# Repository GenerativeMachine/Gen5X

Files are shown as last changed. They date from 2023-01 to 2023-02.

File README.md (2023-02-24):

# Gen5X
Gen5X
Repo for the development of the Gen5X open hardware generatively designed 5 axis 3D printer. 

Imagine a world where machines not only have the ability to design and manufacture products, but they can also create their own updates and upgrades, without any human intervention. The Gen5X is an open-source project aiming to develop self-designing, rapid replicating machines. This repo aims to serve as a resource for researchers in the fields of computational design, AM, and Mechanical Engineering. By open-sourcing this project we hope to foster innovation within the community, and invite you to join us in pushing the boundaries of what is possible with generative design, 3D printing technology, and AI. 

Fusion360 link: https://a360.co/3Y41ZV0 
GrabCAD: STEP files to be uploaded this weekend. 

<p align="center">
  
</p>

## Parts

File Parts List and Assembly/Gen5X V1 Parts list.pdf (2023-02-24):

# Gen5X V1.0

## Parts List

This list of parts includes everything needed to build and assemble the Gen5X Generatively Designed 3D Printer. The V1.0 was designed to work with readily available low cost components. Many of the parts required for this build can be salvaged from older 3D Printers, or similar projects. If you don’t have the right parts (for example LM10UU bearings and 10mm steel rods instead of the specified LM8UU) you could have a go at regenerating the design in Fusion360 to work with your components.

The Fusion360 file can be accessed here: https://a360.co/3Y41ZV0

STEP files have now also been added to the project repo.

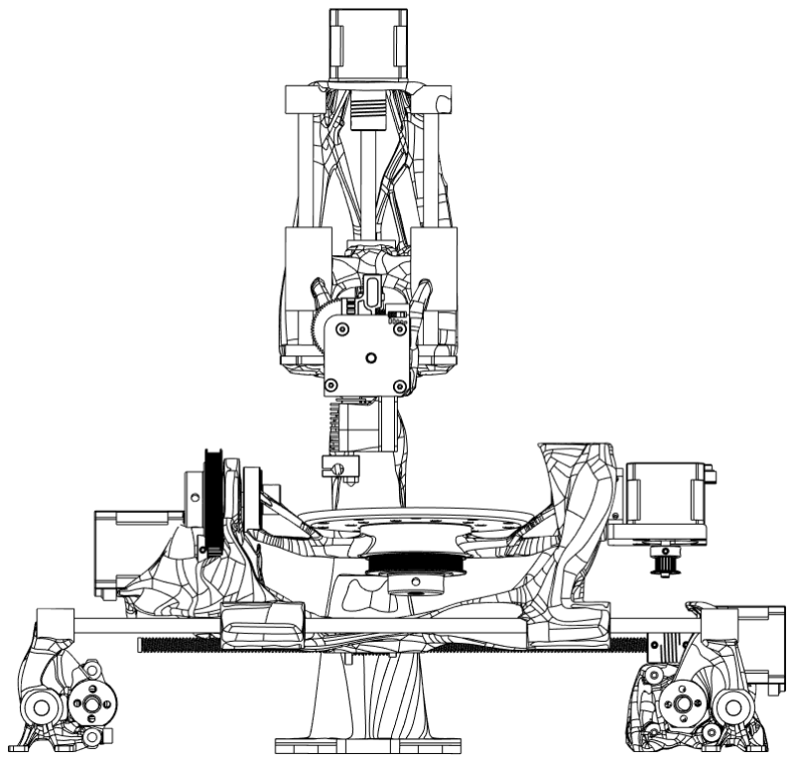
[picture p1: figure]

## Sub-Assemblies

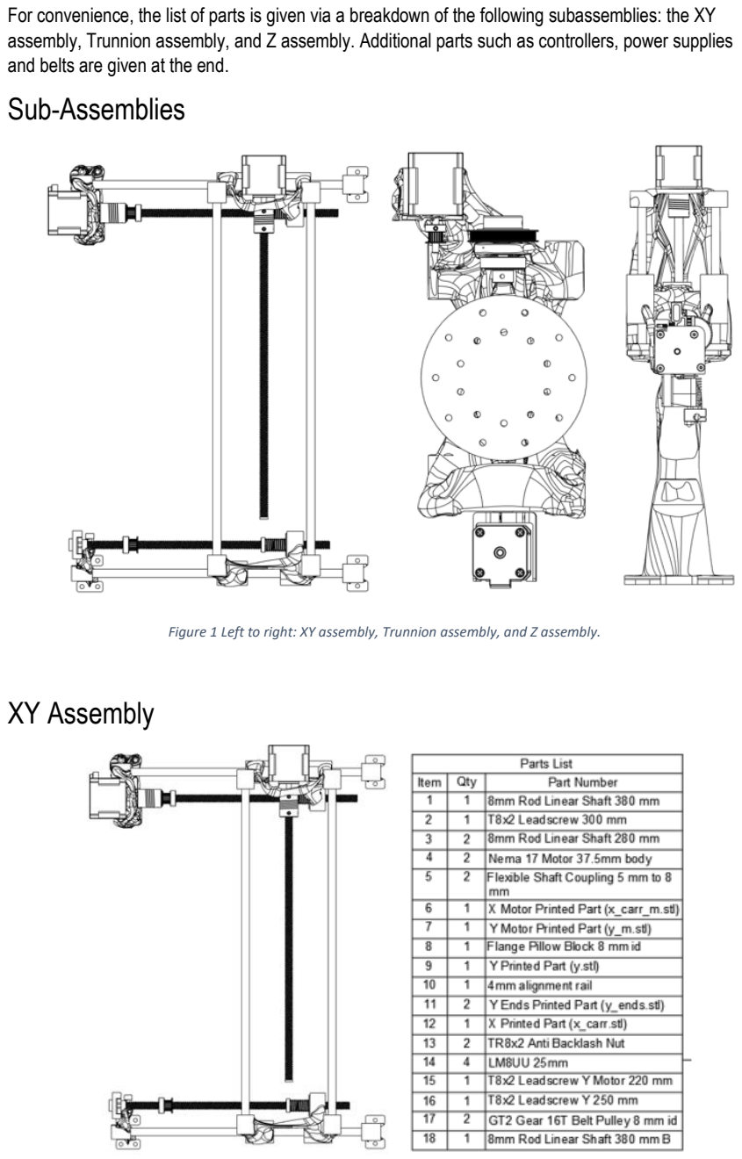
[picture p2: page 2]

For convenience, the list of parts is given via a breakdown of the following subassemblies: the XY assembly, Trunnion assembly, and Z assembly. Additional parts such as controllers, power supplies and belts are given at the end.

Figure 1 Left to right: XY assembly, Trunnion assembly, and Z assembly.

## XY Assembly

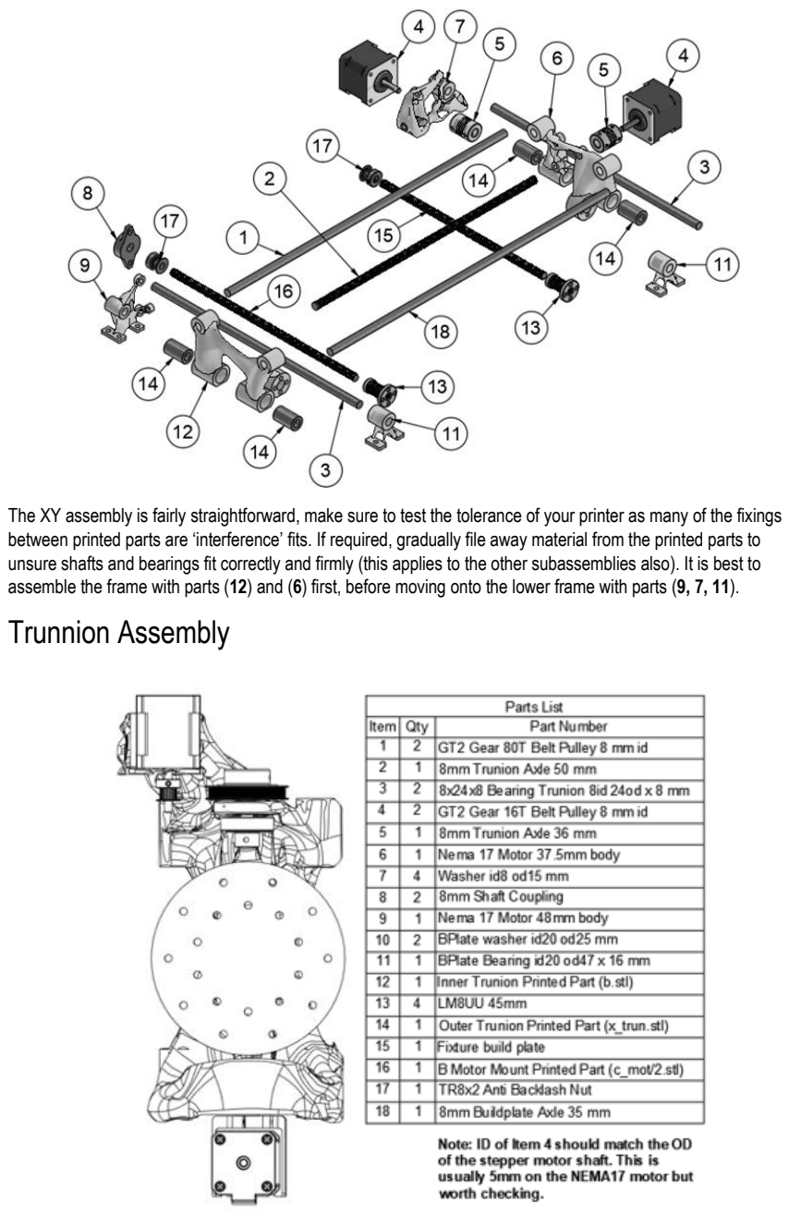
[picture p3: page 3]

The XY assembly is fairly straightforward, make sure to test the tolerance of your printer as many of the fixings between printed parts are ‘interference’ fits. If required, gradually file away material from the printed parts to unsure shafts and bearings fit correctly and firmly (this applies to the other subassemblies also). It is best to assemble the frame with parts (12) and (6) first, before moving onto the lower frame with parts (9, 7, 11).

## Trunnion Assembly

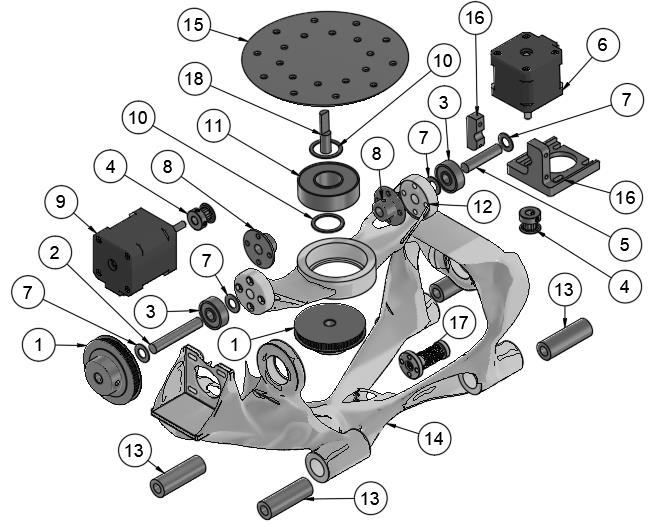
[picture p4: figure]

To assemble the trunnion, firstly press the bearings (3) into the outer trunnion (14) ensuring that the fit is firm. Next, assemble the inner trunnion (12, 8, 11). Fixing (8) to (12) will require four nuts pressed into part (12); using a soldering iron to press these will ensure that the nuts are secure. With part (8) in place, position part (12) between the mounting points in the inner trunnion with spacer washers (7) on the outside (between 12 and 3). Push the respective axles (2, 5) through parts (3) until flush with part (8) and secure.

## Z Assembly and Hotend

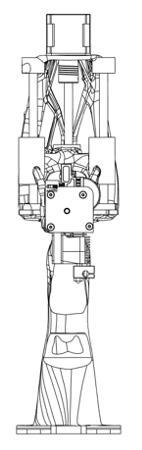
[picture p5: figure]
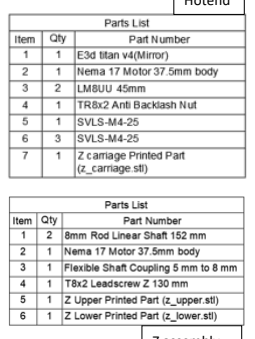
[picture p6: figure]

Z assembly

Hotend

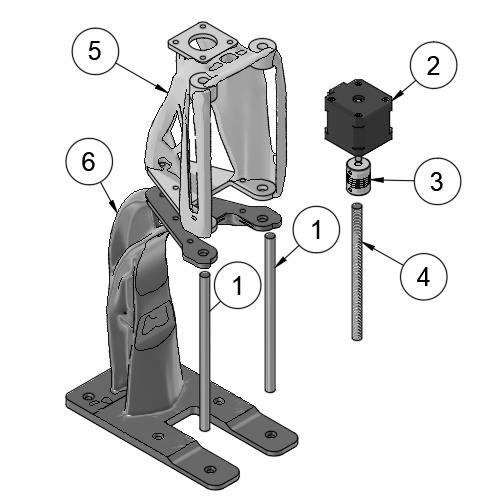
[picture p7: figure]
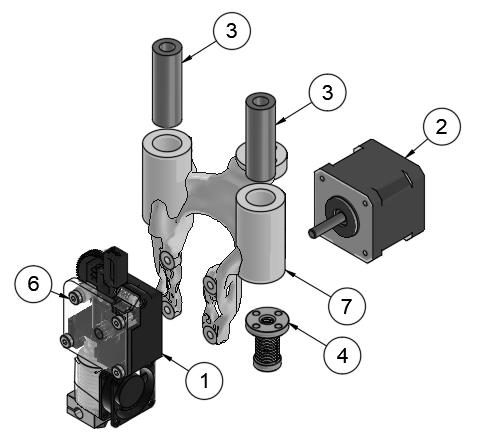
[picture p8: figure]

The Z axis is split into two parts (5, 6) to allow for printing on a broader range of machines. To print the Z axis whole a generative study would need to be redefined as a single piece. Alternatively, parts (5, 6) could be merged in meshmixer before printing. The two parts (5, 6) are currently fastened using M3 or M4 nuts and bolts. Mounting the hotend assembly into the Z axis (5) can be achieved by threading the leadscrew (4) into the hotend backlash nut (hotend 4) before fitting onto half inserted linear shafts (1). Once in place shafts (1) can be pushed though into their positions on part (6). The motor coupling (3) and motor (2) can then be fixed to part (5).

## Electronics


## Belts and Fasteners


(accurate quantities for bolts will soon be given)

Duet 2
DueX5


Meanwell 24v 350W 14.6Amp Power Supply

Belts (Closed Loop) | Qty | Fasteners | Qty
Turntable belt (376 mm) | 1 | M3x8 mm socket head bolts and washers | 40
Trunnion belt (224 mm) | 1 | M3 and M4 Nyloc nuts | 20
Y axis belt (670 mm) | 1 | Assorted length M3 and M4 bolts (10 to 40 mm) | xx

Hotend assembly

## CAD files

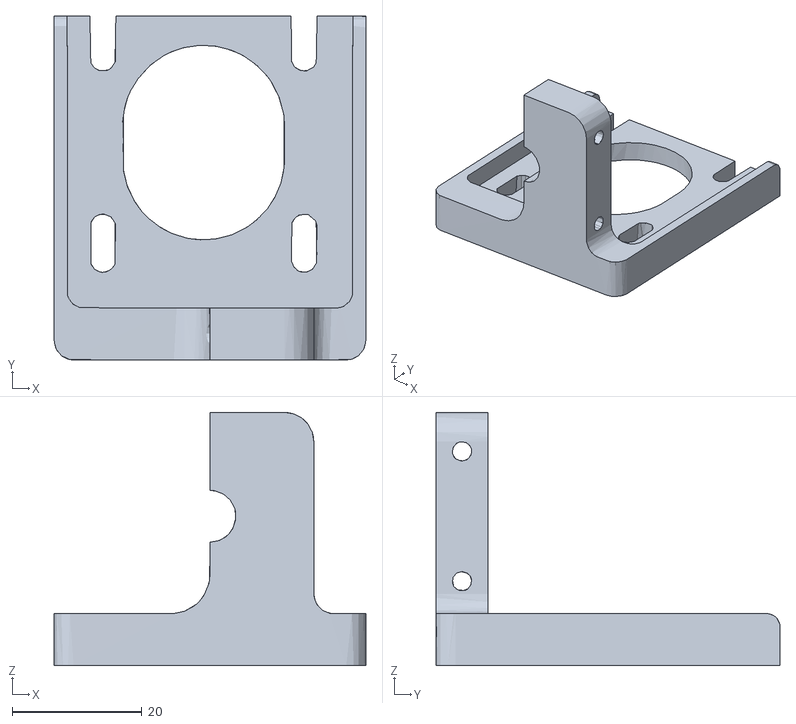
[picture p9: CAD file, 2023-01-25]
Gen5X V1 STL Files/BC Axis/c_mot.stl
48.0 x 53.0 x 39.0

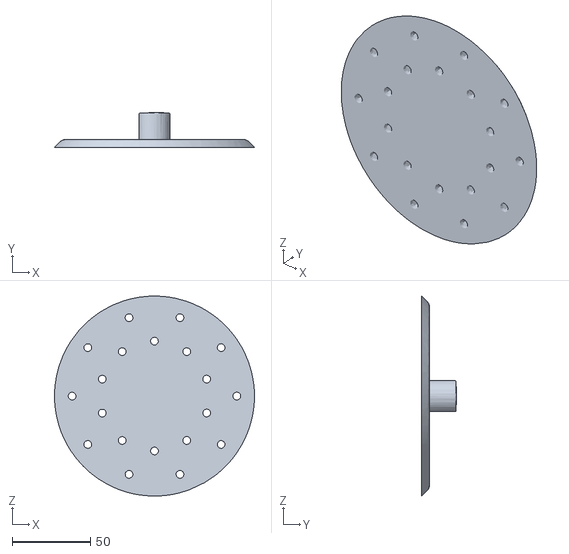
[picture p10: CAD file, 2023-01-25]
Gen5X V1 STL Files/Build Plate/Build Plate.stl
127.5 x 22.0 x 127.4

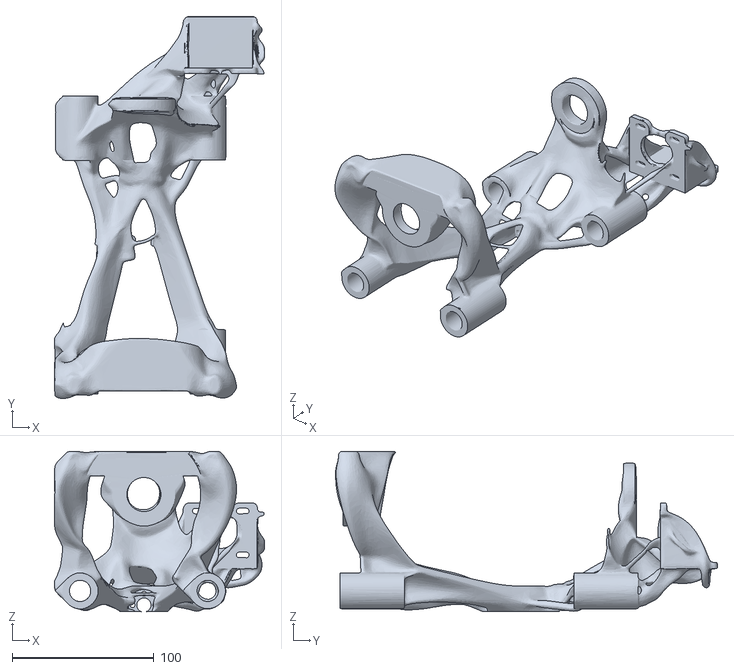
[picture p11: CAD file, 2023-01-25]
Gen5X V1 STL Files/XY Axis/x_trun.stl
148.4 x 269.5 x 113.1

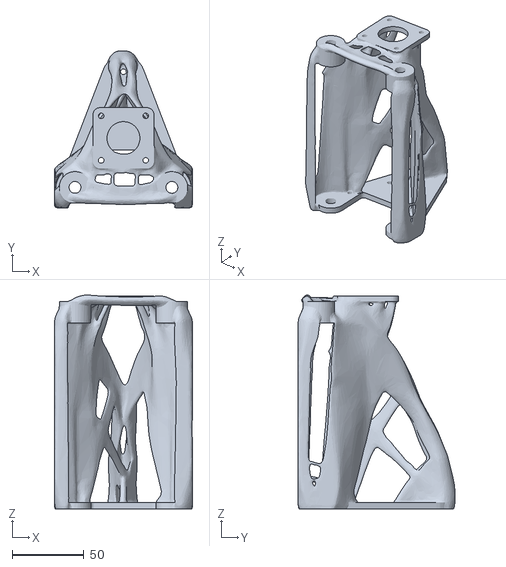
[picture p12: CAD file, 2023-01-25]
Gen5X V1 STL Files/Z Axis/z_upper.stl
96.2 x 109.3 x 149.1

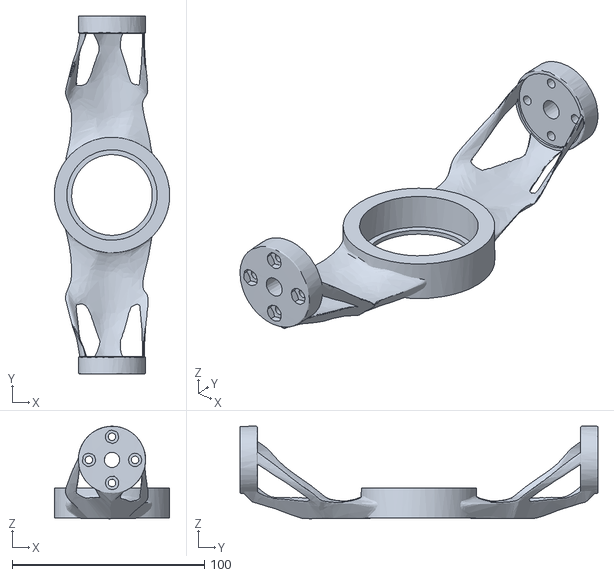
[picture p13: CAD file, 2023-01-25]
Gen5X V1 STL Files/BC Axis/b.stl
60.0 x 186.0 x 48.1

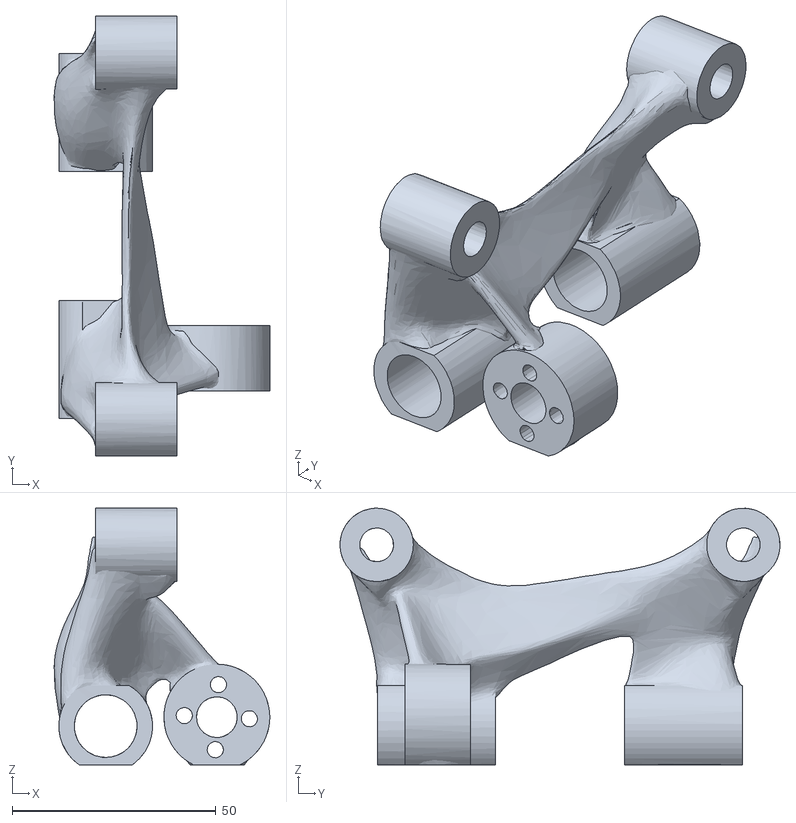
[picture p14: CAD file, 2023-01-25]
Gen5X V1 STL Files/XY Axis/x_carr.stl
52.9 x 108.0 x 63.0

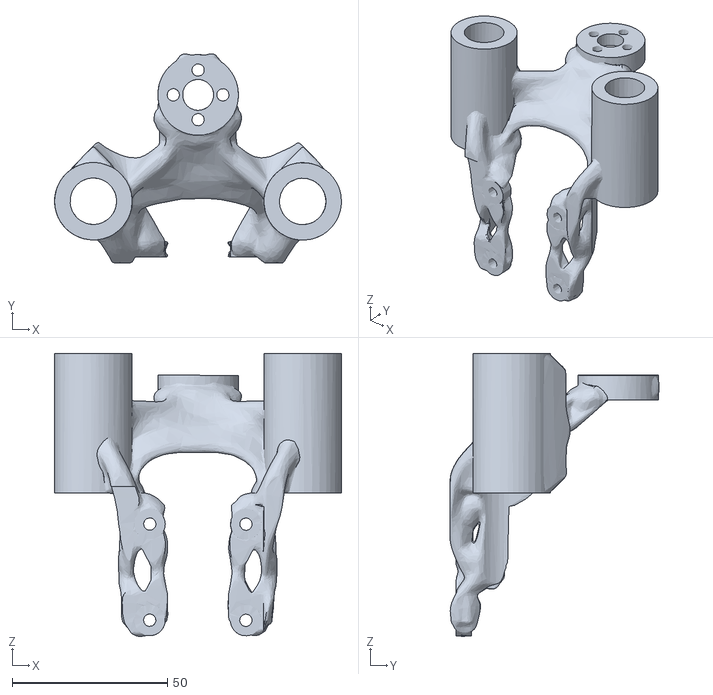
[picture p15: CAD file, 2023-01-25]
Gen5X V1 STL Files/Z Axis/z_carriage.stl
92.5 x 67.5 x 91.3

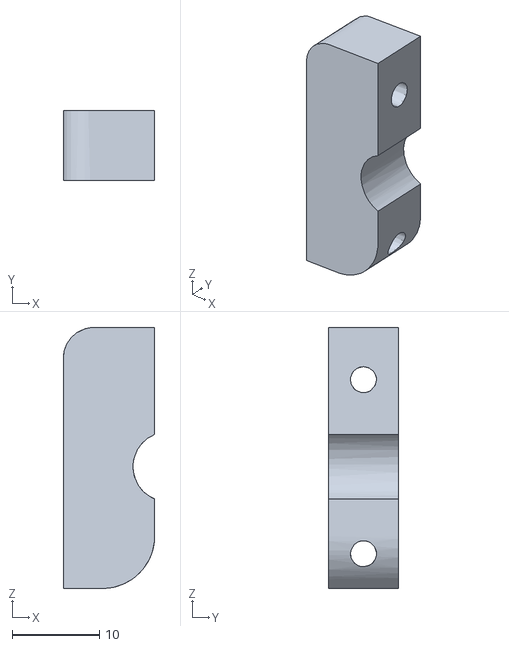
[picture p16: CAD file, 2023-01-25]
Gen5X V1 STL Files/BC Axis/c_mot2.stl
10.5 x 8.00 x 30.0

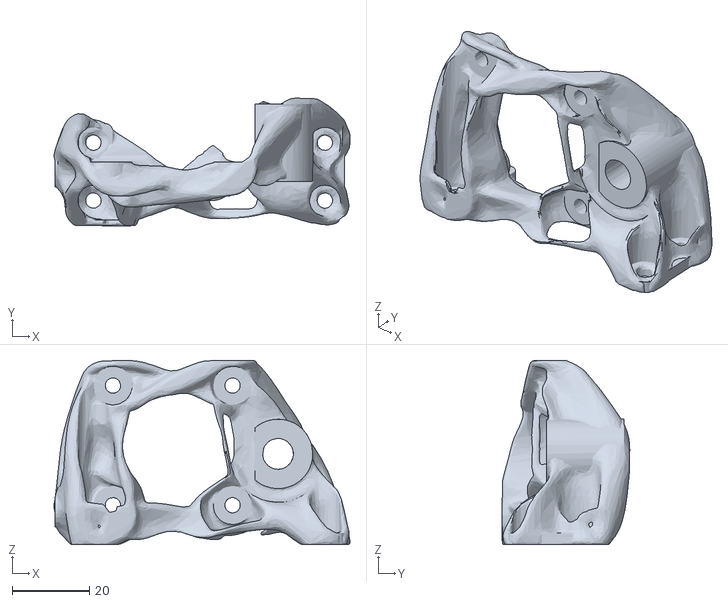
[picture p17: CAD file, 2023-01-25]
Gen5X V1 STL Files/XY Axis/y_m.stl
76.7 x 33.1 x 47.7

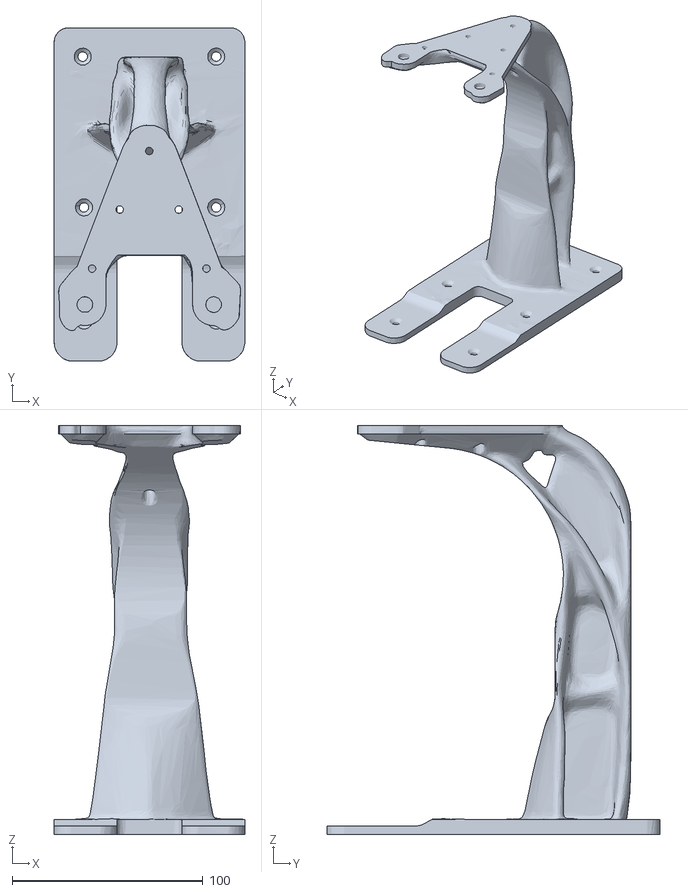
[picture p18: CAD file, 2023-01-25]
Gen5X V1 STL Files/Z Axis/z_lower.stl
100.0 x 174.9 x 214.5

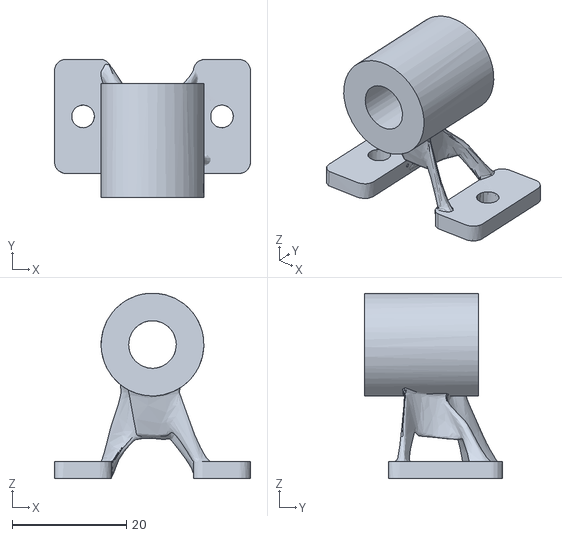
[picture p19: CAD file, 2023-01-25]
Gen5X V1 STL Files/XY Axis/y_ends.stl
34.3 x 24.2 x 32.5

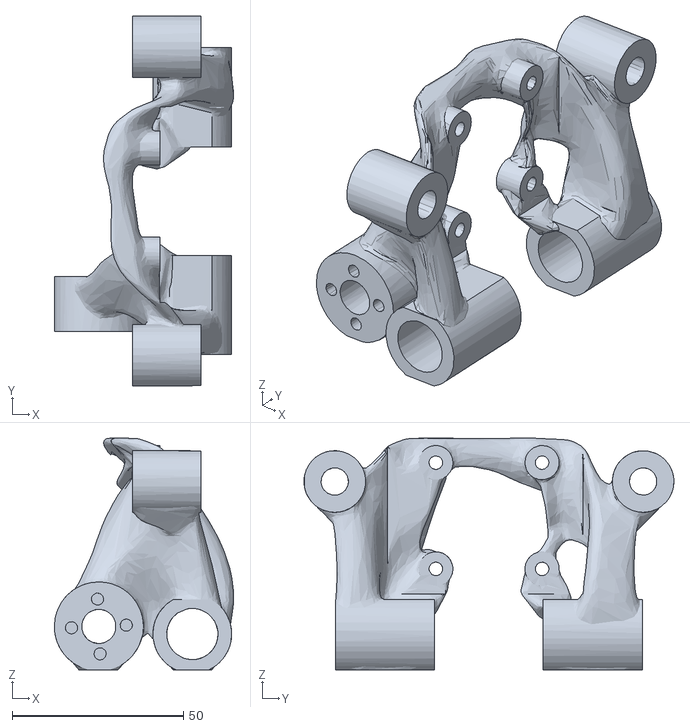
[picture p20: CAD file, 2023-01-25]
Gen5X V1 STL Files/XY Axis/x_carr_m.stl
52.3 x 108.0 x 67.7

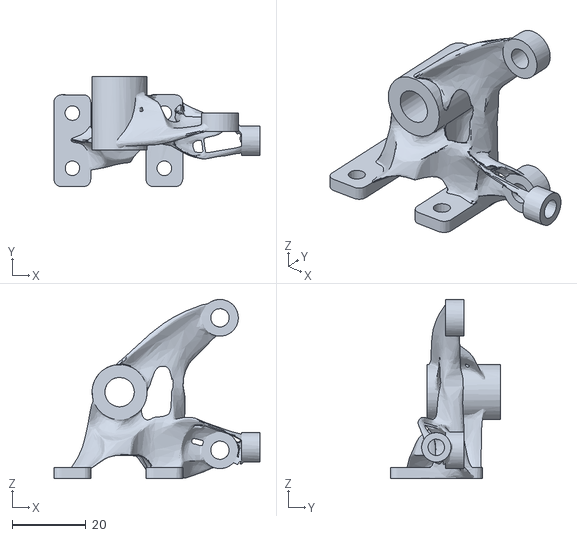
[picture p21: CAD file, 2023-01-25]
Gen5X V1 STL Files/XY Axis/y.stl
56.0 x 30.0 x 48.7

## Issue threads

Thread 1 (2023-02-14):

Assembly STEP file format

yvanblanchard, 2023-02-14:
Hello,

Wonderful project!
Would it be possible to get access to the STEP assembly file, instead of STL mesh files ?
That would ease the building of the assembly in a CAD software (each part already positioned in context).
Moreover, it seems that there are some missing parts (STLs).

Thank you.

glabifrons, 2023-02-20:
Agreed, a STEP would be extremely helpful in not only assembly, but for figuring out what parts are needed (since there's no BOM, issue #2).
It would also make it easier for the community to publish enhancements.

GenerativeMachine, 2023-02-24:
Link to the Fusion360 model now posted on the README doc. This should give you full access to the model and let you download the files in a range of formats.

https://a360.co/3Y41ZV0

Closed 2023-02-24.

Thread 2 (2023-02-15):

Non printed parts

Knotas23, 2023-02-15:
Hello I would like to print and put together a working printer, but I dont know what I need to buy to I can complete this awesome printer. Can you upload non printed parts list please?

FiveStrike, 2023-02-18:
Yeah a BOM would be imminently helpful!

SventeHof, 2023-02-20:
a BOM would be more than helpful!

glabifrons, 2023-02-20:
A BOM is definitely needed, or at least a STEP file (see #1) so we can figure it out.
The tight-zoomed video clips and pictures don't give nearly enough detail.

GenerativeMachine, 2023-02-24:
Just uploaded the BOM and some exploded drawings for the V1.0

Closed 2023-02-24.

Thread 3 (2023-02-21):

Hardware list

Ambro666, 2023-02-21:
How about a hardware list for the stl files. Motors, rods, gears, pulleys, etc, etc

Knotas23, 2023-02-22:
I write it some days ago too. I write him email too And answer Is : (but Its all :-( )
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

Ambro666, 2023-02-24:
this is great now I'll start the project.
    On Friday, February 24, 2023 at 01:38:09 PM PST, Generative Machine ***@***.***> wrote:

Closed #3 as completed.

—
Reply to this email directly, view it on GitHub, or unsubscribe.
You are receiving this because you authored the thread.Message ID: ***@***.***>

Closed 2023-02-24.

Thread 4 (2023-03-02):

x_trun.stl slightly too big for Bambu X1C

divbell, 2023-03-02:
Any suggestions on how to make this printable with the Bambu X1C with a build volume of 256x256x256?

RowboatWilly, 2023-03-02:
Yea, stop using STL's!!!

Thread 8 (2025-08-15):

No access to step files.

ponomarenkode0-create, 2025-08-15:
No access to step files at Autodesk 360. Link to Grabcad not provided. No information regarding the board's switching

carl1961, 2025-09-10:
https://grabcad.com/library/gen5x-1

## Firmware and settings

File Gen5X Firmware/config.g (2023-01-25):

;Gen5X V1 

; General preferences
G90                                         ; Send absolute coordinates...
M83                                         ; ...but relative extruder moves
M555 P2 				    ; Set firmware compatibility to look like Marlin

;Kinematics Profile for 5-axis (cartesian)
M669 K0 X1:0:0:0:0 Y0:-1:0:0:0 Z0:0:1:0:0 U0:0:0:1:0 V0:0:0:0:1

; Network
M550 P"Generative-Machine"                  ; Set machine name
M552 S1                                     ; Enable network
;M552 S2                                    ; Enable AP


;*** Access point is configured manually via M587
M586 P0 S1                                  ; Enable HTTP
M586 P1 S0                                  ; Disable FTP
M586 P2 S0                                  ; Disable Telnet
M575 P1 S1 B57600			    ; Panel Due


; Drive Mappings
M569 P0 S0                                  ; Drive 1 goes backward: X Axis
M569 P1 S0                                  ; Drive 1 goes backwards: Y Axis
M569 P2 S0                                  ; Drive 2 goes backwards: Z Z Axis
M569 P3 S1                                  ; Drive 3 goes forwards: E0
M569 P4 S0                                  ; Drive 4 goes anti-clockwise: U Axis
M569 P5 S0		                                                                                          		    ; Drive 5 goes anti-clockwise: V Axis


M584 X0 Y1 Z2 E3 U4 V5 ; My Driver Mapping

;Microstepping and Speed

M350 X16 Y16 Z16 E16 U32 V16 I1                 			; Configure microstepping with interpolation

; Calculate steps from motor model, U/V set for 80t gearing. 

M92 X100.00 Y100.00 Z400.00 E837.00 U26.667 V35.556 		    ; Set steps per mm and steps per degree
M566 X480.00 Y480.00 Z24.00 E270.00 U480.00 V480.00 P1     	    ; Set maximum instantaneous speed changes (mm/min)
M203 X2000.00 Y2000.00 Z750.00 E1500.00 U2000.00 V2000.00  	    ; Set maximum speeds (mm/min)
M201 X1000.00 Y1000.00 Z1000.00 E1000.00 U1000.00 V1000.00   	    ; Set accelerations (mm/s^2)
M906 X620.00 Y620.00 Z560.00 E1420.00 U1300.00 V1300.00 I10            ; Set motor currents (mA) and motor idle factor in percent
M84 S30                                    			    ; Set idle timeout


;Axis Limit
M208 X-126:125   Y-92.3:50  Z125:-1 U-200:200 V-12000:12000					; Centre of the rotating bed is set to origin 0,0
M564 H0								; allow unhomed movement


; Endstops for each Axis
M574 X1 S3				 ; Set endstops controlled by motor load detection
M574 Y1 S3                               ; Set endstops controlled by motor load detection
M574 Z2 S4                               ; configure sensorless endstop for high end on Z (Detected by two motors)


; Stallgaurd Sensitivy
M915 X S3 F0 H400 R1		                ; Set X axis Sensitivity
M915 Y S3 F0 H400 R1		                ; Set y axis Sensitivity
M915 Z S3 F0 H400 R1		                ; Set z axis Sensitivity


; Z-Probe (manual)
M558 P0 H15 F120 T6000                          ; disable Z probe but set dive height, probe speed and travel speed


; Heatbed Heaters and Thermistor Bed 
M140 H-1 ; Disable heated bed

; Filament Sensor Port and Loading Feature ON
;M950 J1 C"e0stop" ; Input 1 e0 Filament Sensor ; Filament settings turned off 
;M581 P1 T2 S0 R0 ; Filament Sensor P1 triggers Trigger2.g always (R0)

; HotEnd Heaters and Thermistor HotEnd           
M308 S1 P"e0temp" Y"thermistor" T100000 B4725 C7.06e-8 ; sensor 1
M950 H1 C"e0heat" T1					; Create HotEnd Heater
M307 H1 R3.440 K0.388:0.000 D15.13 E1.35 S1.00 B0 V24.4 ; set the process parameters for heater 1
M143 H1 S285                            ; Set temperature limit for heater 1 to 285C HotEnd
M302 S185 R185

; Fans
M950 F1 C"Fan1" Q250				; Creates HOTEND Fan
M106 P1 T45 S255 H1                 ; HOTEND Fan Settings
M950 F0 C"Fan0" Q250				; Creates PARTS COOLING FAN
M106 P0 H-1                         ; Set fan 1 value, PWM signal inversion and frequency. Thermostatic control is turned off PARTS COOLING FAN

; Tools
M563 P0 D0 H1 F0                            ; Define tool 0 Heater Block 1
G10 P0 X0 Y0 Z0                             ; Set tool 0 axis offsets
G10 P0 R0 S0                                ; Set initial tool 0 active and standby temperatures to 0C
